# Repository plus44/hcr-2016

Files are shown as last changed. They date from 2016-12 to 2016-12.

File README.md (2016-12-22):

# Human-Centred Robotics 2016

##### Xavier Laguerta-Soler, Periklis Korkontzelos, Nathan Warner, Mihnea Rusu
##### {xl5512, pk1913, njw13, mr3313}@ic.ac.uk
##### *Imperial College London*

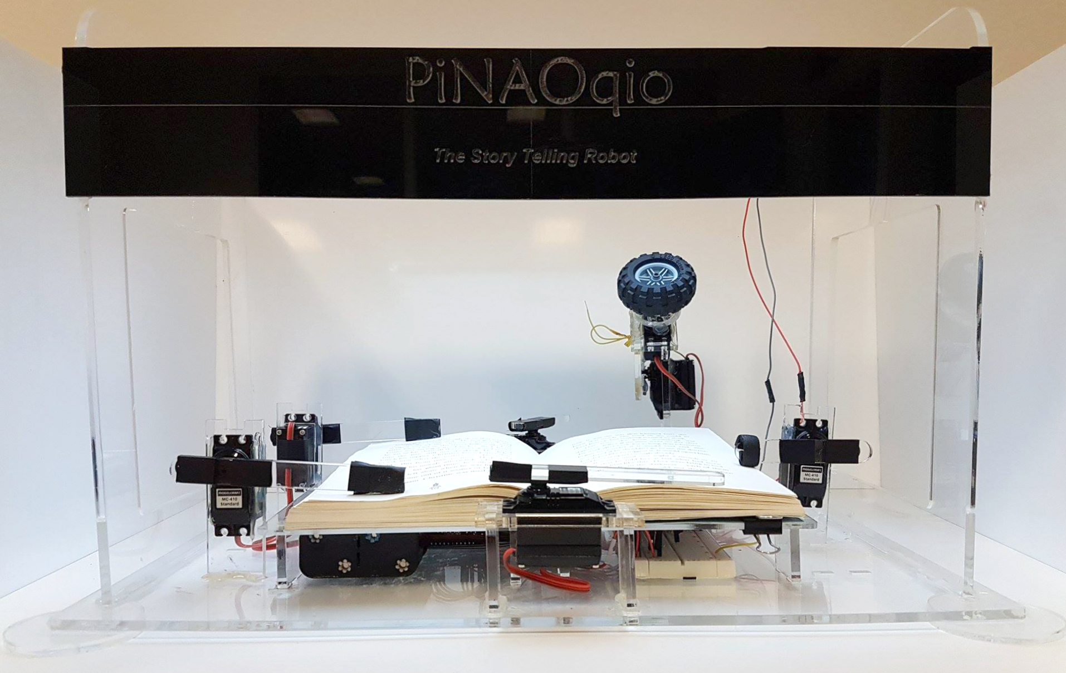
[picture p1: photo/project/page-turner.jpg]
PiNAOqio Page Turner (https://www.youtube.com/watch?v=8CyoGCQ_uKY)

Video :video_camera: link: https://www.youtube.com/watch?v=8CyoGCQ_uKY

Our project is about building an interactive story-telling robot that reads (and turns the pages of) physical books to children :baby:. Our robot, **PiNAOqio**, uses the [NAO robot](https://www.ald.softbankrobotics.com/en/cool-robots/nao) from SoftBank Robotics to interact with the reader through speech and gestures. An additional hardware rig was designed and built to turn the pages of books and to accommodate a camera for capturing the open leaf. 

As this was first and foremost a research project, we set out to test the hypotheses proposed in our initial report, the [design report](docs/reports/design-report.pdf). Evaluation sessions were held, where participants were presented with 3 different instances of our system with varying degrees of capability and were read a short passage from the same book :book: by each. In response, their task was to complete a brief questionnaire.

The full system is comprised of the following components: a laptop :computer: to interface with NAO, the robot, and to perform optical character recognition (OCR) on the picture of the book; a Raspberry Pi to control the page-turning mechanism; an iPhone :iphone: (6 or higher) to photograph the open book, and a server on the cloud to enable communication between the different platforms. As will be apparent to the reader, our system architecture ended up being quite different (and more complex) in the [final report](docs/reports/final-report.pdf) to what we initially envisioned in the design report, mainly due to complications with the OCR setup.

Ultimately the project was a success :clap: - the high-risk components namely the page-turning mechanism and OCR functioned to a high standard and the results of our research suggested the proposed hypotheses :+1:.

## Contents

This repository is composed of the following directories:
  - **[app](app)** iOS app source code and Carthage dependencies.
  - **[docs](docs)** System startup documentation and reports written for this project (including the individual reports).
  - **[eval](eval)** Evaluation questionnaires handed out to the participants of our study and a Matlab script to determine the results of our experiment.
  - **[hardware](hardware)** Laser cutting files for the page-turner.
  - **[scripts](scripts)** A number of useful, but maybe messier scripts for quick or intermediate testing.
  - **[sdk](sdk)** The correct version of the NAOqi SDK that works with Python.
  - **[src](src)** Source code (in Python) for all individual elements of the system, along with a pip requirements file for setting up (a partially working) virtual environment. Each component is meant to have a copy of its respective subdirectory. The [phone](src/phone) component is only a networking-enabled dummy, as the real phone component is the iOS app.
  - **[photo](photo)** Test photographs of various book poses and lightings (for OCR) taken throughout the course of our project, along with a dedicated file, *[latest.jpeg](photo/latest.jpeg)*, that the laptop client updates while it's running, with fresh images received from the phone.

Link to the Python library used for [speech](https://pypi.python.org/pypi/SpeechRecognition/), which is not included in our virtual environment requirements file due to platform mish-mash :disappointed:.

### Quick links:
  - [Design Report](docs/reports/design-report.pdf)
  - [Final Report](docs/reports/final-report.pdf)

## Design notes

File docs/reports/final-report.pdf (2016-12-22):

## PiNAOqio: Research into Interactive Story-Telling Using Robots and Physical Books

Xavier Laguarta Soler (xl5512), Periklis Korkontzelos (pk1913), Nathan Warner (njw13), Mihnea Rusu (mr3313) Imperial College London

Abstract
This paper evaluates the effectiveness of the interactive
robot storyteller PiNAOqio, boasting the ability to turn the pages of physical books and deliver contextualized gesticulations. An assessment was conducted on 23 volunteers whereby PiNAOqio was pitted against both a static implementation and an audiobook. Performance was measured in terms of information retention and user enjoyment, finding PiNAOqio to be just as, if not more effective than the audiobook across our given test population. Further developments and enhancements are proposed to be implemented in the near future.
I. Introduction
Reading is an integral and fundamental aspect of a child’s education and has been shown to have a significant influence on their development (Freire & Slover, 1983). In today’s digital era the ways through which children are
introduced | to | books | and | written | content
is constantly evolving, placing an increasing prevalence on digitized content and stepping away from traditional hard-copy books. PiNAOqio proposes a new and innovative means to bridge this gap and engage children with literature. Utilizing a synergistic collaboration of an automated page turner, optical character recognition (OCR) algorithm, intelligent gesture association engine and voice recognition, PiNAOqio is well poised to revolutionize conventional story time.
With users being able to load their own pre-existing volumes, PiNAOqio will be versatile enough to be deployed in a range of situations and environments. We feel that children that have to be hospitalized for long periods of time, in particular, would stand to receive the greatest benefit from this technology. Not only
will PiNAOqio be | able | to | read | them
their favourite stories, he can also serve as a companion, supplementing the limited human interaction they are likely to receive and alleviating some of the stress and anxiety these children are prone to experience (Lau, Bernard and Wilson, 1993). Although PiNAOqio is not intended to be a tantamount replacement to a genuine human storyteller, he is anticipated to make story telling a more fun and social experience for young listeners.

II. Hypothesis
The aim of this project was to investigate the effectiveness of a “storyteller robot” as a source of engagement and educational entertainment for children. In order to quantify whether this goal has been achieved, user experience and the ability to retain information were measured. Upon this basis, the subsequent hypotheses are assessed. These figures have been approximated to indicate thresholds for satisfactory performance:
a) Story-telling by PiNAOqio will improve information retention and user experience by 15% and 30% respectively in comparison with story-telling by an audiobook.
b) Making gestures to emulate a human story-teller in conjunction with an active interaction with the user will improve the retention of information and the user experience by 10% and 20% respectively.

III. Related Work
The concept of an interactive storytelling robot has been approached by other groups in the past; equally, there exist several page flipping mechanisms for the purpose of digitizing hard copy books (Qumsiyeh, 2016 and Charlton, 2015). However, an implementation that uses both of these in tandem has heretofore not been attempted.
An instance of a comparable system, The Storytelling Companion, designed by the Personal Robotics Group at MIT (Kory, 2016), was developed as a social character relating to children as a peer through a storytelling game. This game is played on a tablet and the aim is to improve language and vocabulary skills in early stages in life. Another example is TROBO – the storytellinsg robot (TROBO, 2016), a plushy robot that connects to a smartphone or tablet application and tells an education story from a library.
The fundamental drawback to these currently available solutions is that they rely on a tablet to function. Long-term use of tablets and other such devices have been shown to have a detrimental impact on young children, such as addiction. The positive to this approach is that it utilizes technology the user is already likely to own, thereby largely reducing the overall cost of the product.

IV. System Design

### 1. Overview

From our previous report (Laguerta, Korkontzelos, Warner, & Rusu, 2016), the system has increased in complexity as we discovered insufficiencies with the old setup that would disrupt our desired user experience. Formerly we decided that a Raspberry Pi 3 should act as the main controller, communicating with the NAO robot, page-turning mechanism and camera. Such a setup would have been simpler to execute, and would have yielded a more portable prototype at the cost of limited opportunity for expansion and improvement past basic functionality. The major problem with this setup was the poor quality of the official Raspberry Pi camera for our purpose of optical character recognition (OCR).
Our first attempt at solving the problem of the camera, mentioned in one of our individual reports (Rusu, 2016), was to install a light-plate fashioned from a liquid crystal display (LCD) backlight directly above the book. While this boosted the accuracy of OCR slightly, we were still troubled by the shallow depth of field of our camera, which made it so that only a handful of pages could be turned before a (manual) refocus was needed. After experimenting with exposure settings and filter parameters on the Raspberry Pi camera, we were ultimately unable to produce reliable, repeatable OCR results.
Brief experimentation with an iPhone camera using the existing rig resulted in OCR accuracy figures of approximately 90% following brightness and contrast image enhancement filters. This observation led to our decision of using a smartphone as the camera, despite the increase in system complexity posed. At this point, the Raspberry Pi was only required for controlling the page-turning action; as such, we decided it would be best that a laptop with far more computational power than a singleboard computer handled the OCR engine and communications to the NAO robot. An iOS app would be needed, as well as a means for transmitting images from the phone to the laptop and page-turning instructions from the laptop to the Pi board.
The final system was comprised of five elements: iPhone, Raspberry Pi, laptop, the NAO robot, and a server running on the cloud as an Amazon Web Services (AWS) instance to enable communication between the components. A high-level diagram of the system is shown in figure 1. Communication to the server is done via (Hypertext Transfer Protocol) HTTP. The role of the server is to manage the data being transmitted to each serverconnected device given what has been received from all devices up to that point in time.
Devices operate in half-duplex mode: either transmitting or receiving. During autonomous system operation only two of three devices should ever be simultaneously in receive mode on the network, otherwise the system reaches rest. Receive mode utilizes a technique known as HTTP long-polling that reduces the amount of unnecessary network traffic when polling for data. The client begins by sending a request for data from the server, to which the server only responds after data is available for that device or a time-out has occurred (in which case the request should be re-initiated). Devices expect to receive single actions from the server, thus the data being transmitted is simply the action, or data object (e.g. image) as a string. Transmission data is sent using (JavaScript Object Notation) JSON strings in the body of the HTTP requests.

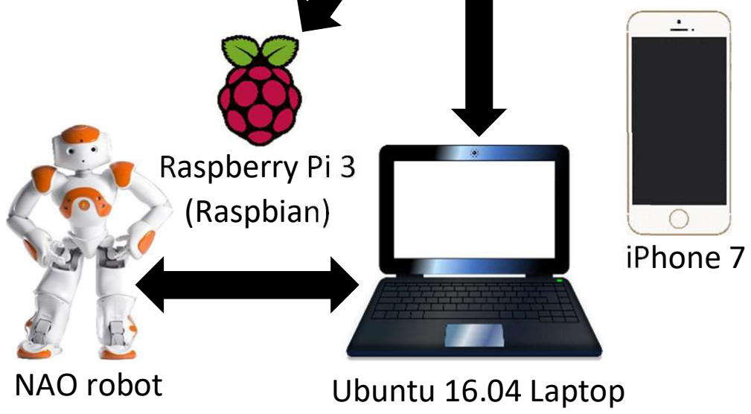
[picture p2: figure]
Raspberry Pi 3 (Raspbian); iPhone 7; NAO robot; Ubuntu 16.04 Laptop

### 2. Server

The elements of our system need a way of communicating with each other in an organized manner in order to emulate the behavior of a state machine. One thing all our components have in common is a network connection – the obvious facilitator for our goal is thus a centralized hub (or server) to which all devices report updates to their state. A t2.micro Elastic Compute 2 (EC2) instance on AWS running Ubuntu 16.04 was used as the platform for our server. The cloud server route was taken due to the hosting restrictions imposed on the college network. With access to an isolated network, the server component can be integrated within the laptop component and the system design simplified.
Python was used to implement a multithreaded HTTP server with three valid addresses: /pi, /phone and /laptop. The HTTP protocol defines several possible request types

AWS Server

Figure 1 - System High Level Diagram that may be sent by a client device. Of importance for our application are the GET and POST requests. A GET request to one of the aforementioned addresses initiates the long-polling process, and the server would only fulfill the request if data is available for that device or the time-out threshold has been reached. Multithreading is necessary for handling long-polling as this is a blocking operation, meaning the thread of execution is blocked until a result is available. POST requests from a device to the server contain JSON data about the state of that device. The JSON fields are specific to each device and are agreed upon by both the client and the server before runtime.
State machine functionality is emulated on the server through (First In First Out) FIFO queues. JSON data combinations from a device’s POST request produce one or more work items, or actions, that need to be passed on to the other devices. Each device has its own FIFO queue of work items; the resulting actions are pushed on the corresponding device’s queue. When a device long-polls the server and its queue is not empty, the first element on its queue is popped and parsed in the body of the HTTP response.
Emulating a state machine as such offers a high degree of modularity and flexibility in adding functionality to the system as a whole. Additional JSON fields may be defined for a device, as well as the work items they generate. Handling the new functionality can be implemented simply on the respective target device side

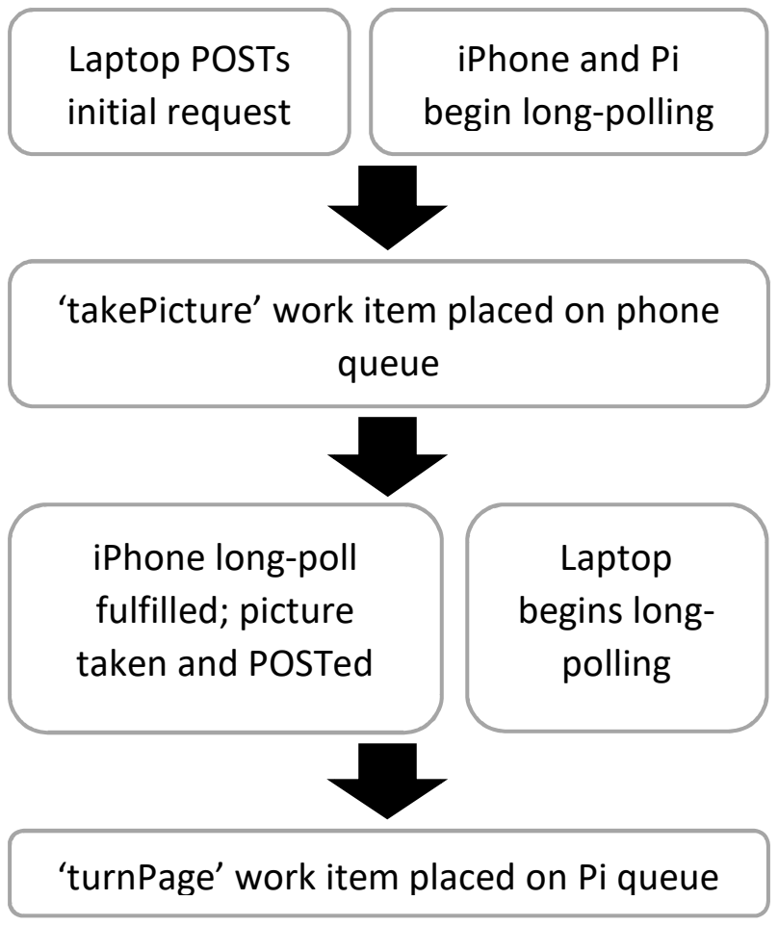
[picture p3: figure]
Laptop POSTs initial request; iPhone and Pi begin long-polling; ‘takePicture’ work item placed on phone queue; iPhone long-poll fulfilled; picture taken and POSTed; Laptop begins long- polling; ‘turnPage’ work item placed on Pi queue

by scripting the desired action in response to the received work item. Before deploying the server, we first ensured successful operation using dummy clients on the physical laptop. Example operation from rest is briefly shown in figure 2.

### 3. iPhone App

There are two main tasks the iPhone element of the project must perform: capture and filter an image using the rear-facing camera; and implement the functionalities of the phone client. A skeleton camera app, written in Swift, provided by an online article [Caldari, 2015] was used as a starting point. Since modern iPhones feature powerful Graphics Processing Units (GPUs), we decided to take advantage of said feature by firstly configuring the base app to use the GPU pathway for rendering the image, and secondly to filter the shot on the GPU. This enabled a real-time post-filtering viewfinder that did not introduce any visible lag to the graphical user interface (GUI), even on an older generation GPU-equipped handset.
In terms of image filtering, the Apple iOS Core Image library provides a large number of GPU filters, with easily configurable parameters as well as the option of userwritten kernels in a limited version of the OpenGL language. Our final filter stack was composed of a saturation reduction filter (for converting the image to black and white), followed by brightness and contrast booster filters and ending in a custom GPU kernel for a thresholding filter. The thresholding filter determines whether the intensity of a given pixel is below or above one of two thresholds. When below the respective threshold, the pixel is forced to black; when above, the pixel becomes white. Even without our dedicated lighting rig, OCR accuracy levels of 100% were common occurrences in our experiments, proving to us that switching to the iPhone camera was indeed the right choice.
Client-side code was written using the aid of the Alamofire networking library and the SwiftyJSON library for generating the JSON inside the POST request to the server. Instructions for only a single server action were provided – ‘takePicture’, and only a small number of data fields were required. The filtered image was sent across to the server as a base-64 encoded string in the JPEG format with minimal compression factor, under the ‘picture’ data field of the JSON POST request. Previously (Rusu, 2016), we mentioned requiring lossless compression for the picture on the Raspberry Pi camera, however this proved to be unnecessary in the case of the higher quality iPhone camera.

### 4. Raspberry Pi

The main role of the Raspberry Pi is to sequence the servos of the page turner in order to flip pages of the book, when instructed to do so by the server. A secondary role

Figure 2 - Example System Operation of the Pi is to control the brightness of the lightplate in order to improve OCR performance. However, given the speed and accuracy of the iPhone camera’s auto-exposure function and the performance of our filter stack, we found that the only use of this functionality is to preserve battery life. In the final prototype, the Pi was not to be connected to a screen, mouse or keyboard therefore we created passthrough modes on the server and laptop sides that would allow control over it out of story-telling context. Multithreading was used to enable control of several servos in parallel. One problem we faced was with the built-in (General Purpose Input-Output) GPIO library on the Raspberry Pi. This library is not designed for multithreaded operation, and as a result we were troubled by segmentation faults when trying to access the same servo multiple times in a program. Happily, the solution was simple - run each set of parallel servo operations as a standalone script.
As in the case for the other devices on our network, the Pi requires client-side code that mirrors what the server expects from it and reacts to all possible actions received from the server. Since the mechanics of the page flipper have no way of feedback, a way for the laptop to adjust a small set of servo parameters was needed as the robot would reach further into the book. Fortunately, the software architecture allowed us to implement this with ease, by defining new work items for the Raspberry Pi, together with the corresponding JSON fields on the laptop side.

### 5. Laptop

Arguably the central element of our system was the laptop. Its responsibilities included: speech processing the user’s voice greetings and commands through an external microphone; requesting images from the server; doing OCR on images of text from the book; parsing gestures into the text obtained from OCR; and lastly controlling the NAO robot. A state machine was in charge of requesting server data and performing the operations in the needed order.
As for the case of the Raspberry Pi and the server, Python was used for writing the laptop code. The C++ based OCR engine Tesseract proposed in the analysis of one of our individual reports (Rusu, 2016) was used in the final prototype. Thanks to the library’s popularity in the open-source community, a Python wrapper was readily available for it. An outdated version of the NAOqi Python Software Development Kit (SDK) was used, as the most recent official one at the time of writing was not functional. Thankfully, we were not missing any features of the newer library to complete our project. Finally, user speech processing was handled using the latest official Python Speech Processing library.
In our design report (Laguerta, Korkontzelos, Warner, & Rusu, 2016) we mentioned the need for doing the page turn and OCR with a short time in advance such that NAO can speak without interruptions. Due to NAO’s speaking and OCR being blocking operations, multithreading was required to achieve this purpose. Unfortunately, due to time constraints with the project we were unable to implement this feature. However, thanks to the high performance laptop used, the delay between an image being received and OCR being complete was reduced compared to the alpha prototype featuring the Raspberry Pi as the main controller.

### 6. Page Flipper

The page flipper module is required to flip the pages of the loaded volume once it receives its cue from the server, allowing for a seamless transition in the flow of the passage. Each turned page will need to be presentable enough for OCR to take place, entailing minimal creasing and curvature. A custom servo actuated mechanism was designed and built, with each servo operated sequentially, modelled as a state machine on the raspberry Pi. The system receives an action request from the server, the sequence executes and then awaits its next command. The sequence is shown in figure 3, below.

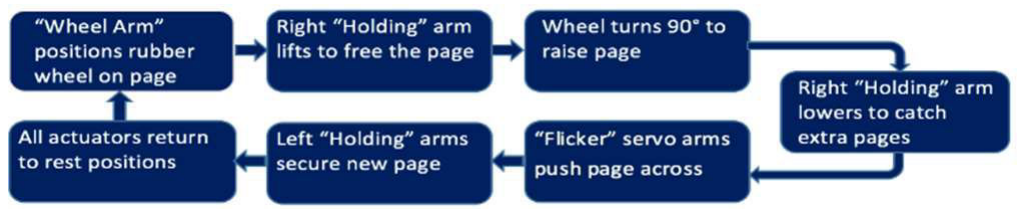
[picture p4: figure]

Figure 3 - Page Turning Sequence for Servos
The pivotal component of the system is a small rubber wheel that produces traction in order to lift the page. After passing through several iterations and permutations, the final mechanism to accomplish the page turning utilised seven servo actuators, these are illustrated in figure 4.

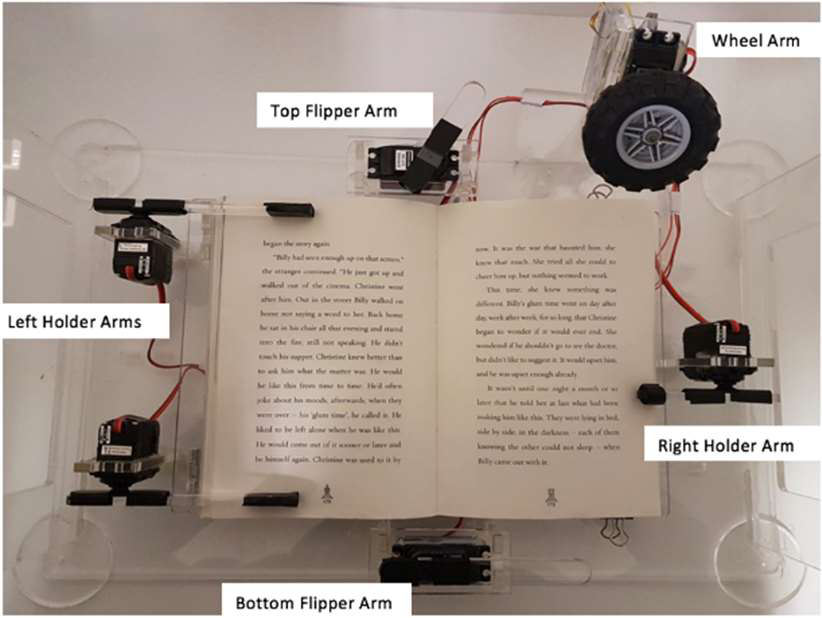
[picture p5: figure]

Figure 4 - Final Design of Page Turning Module

The whole module was made wireless and portable, using an 11.1V Lithium Polymer battery to power the light plate, with a 5V buck converter to supply both the servos and Pi. The entire assembly was constructed from 5mm laser cut acrylic, allowing for both a stylistically pleasing and structurally functional design, as well as fast development time. Once loaded by the user with any standard size fiction text and properly calibrated, the system was capable of autonomously turning in excess of

### 10 consecutive pages without error. The final system

assembly is shown in the appendix.
Although the page flipping was shown to work well, there are several potential enhancements through which the performance could be improved significantly. Namely, feedback could be introduced on the wheel using a micro load cell, allowing it to consistently assert the appropriate amount of force on the page. For testing the ideal wheel height was determined experimentally, programmed into the system and adjusted as needed. The drawback to this approach is that the angle by which the wheel came down by had to be user adjusted every 10 pages or so as this height changes. Another weakness with the current configuration is that there is considerable jitter in the servos. Since we are using a software based controller, the timing of the pulses sent to the servos is likely to be thrown off by other processes running on the operating system. To circumvent this, it would be advantageous to control the servos instead using hardware; this can be done using a dedicated PWM chip, such as PCA9685 that interfaces directly with the Pi via hardware I2C.
In addition, with the current setup two or more pages may be turned at once due to irregularities in the binding of the book, pages being stuck together, or the wheel asserting too much force. Currently the system has no means to deal with this eventuality. One possible approach could be to keep track of the page numbers involves the OCR module. If an inconsistency in the page count is detected, PiNAOqio can then alert and instruct the user to turn back to the correct page. Better yet would be the ability to actively check and detect whether more than one page has been lifted and turn back to prevent the error from occurring. Commercial printers are faced with a similar challenge, some transmit ultrasound through the page and measure the transmission coefficient, thereby any discrepancy in this reading can trigger an error condition.

### 7. Gesture Controller

The NAO robot is controlled by a gesture controller, which is implemented as a python class. The gesture controller interfaces between the laptop and the robot and is responsible for implementing all talking and gestures made by PiNAOqio during initial interaction and storytelling, using the API (Aldebaran, 2016) provided by Aldebaran.

The gesture controller is initialized along with the main program at the initialization of the main state machine. In the initialization phase the motors of the robot turn and PiNAOqio stands up to signal the user that testing is about to commence. In addition, the desired pitch, speed and volume are set to their default value.
For the initial interaction, the gesture controller is passed to the speech controller module and called upon whenever needed, to avoid the risk of runtime errors whereby more than one modules try to access the NAO robot. The questions and responses of PiNAOqio during this phase are predetermined and thus, a text-to-speech function handles the articulation of responses. At the same time, the BodyLanguageMode is set to ‘contextual’ and allows the robot to make gestures that can be associated with the responses given. This is a built-in function from the NAOqi API and works on a basis of a dictionary associating words with gestures. This is not optimal as some gestures appear to be out of context, yet it enhances the animacy and likability of the robot, which is the aim. During storytelling, the gesture controller is being used for the fully interactive and the non-interactive robot versions. For the non-interactive version, only the text-tospeech function is being used as no gestures are required. In order to acquire statistically meaningful data for the evaluation of the hypothesis, it is required that the fully interactive version PiNAOqio emulates a human storyteller as closely as possible. Thus, the
‘contextual’ BodyLanguageMode is | not | adequate
but two more dictionaries associating key words/phrases with gestures are built to provide a more refined gesture library. The first library is built using some already available gestures that accompany words such as “me”, “you” and “I don’t know”. To further enhance the animacy of PiNAOqio custom gestures are added by defining joint angles as a function of time through choreograph. These gestures are more specific and complex to generate including gestures to “wipe forehead” or change eye colour LED, so the custom dictionary was optimized for the specific, fully-interactive passage.
A string parsing algorithm has also been developed as part of the gesture controller and is responsible for handling the gestures of custom built dictionaries. Before the interactive storytelling commences, the story string is parsed according to key words and phrases of the two dictionaries. The gesture controller is then able to determine the timing and the place to input gestures associated with speech.

### 8. Speech Recognition

A speech interaction component, Speech Controller, was introduced to the interactive version of the robot before the reading began. Aside from basic salutations, the interaction allowed for the robot to get feedback on the user whether the volume and speed were fine or should be changed before the reading began.
This was implemented as a python class, which was called from the main state machine at an initial stage. Google speech was used as the speech processing tool, as it gave the highest accuracy when compared to other easy to implement tools, such as sphinx. Once the speech was recognized, the string of text was checked with a dictionary in order to detect the key words in each sentence, which varied as the conversation progressed. Depending on the result, one answer or another would be given by the robot, along with a specific action if required, such as increasing the volume or speed of speech.
V. Experiment
Pinaoqio was tested over the course of three days in room 508 of the EEE building in Imperial College London to have a testing environment of complete silence. Keeping a low noise level was important for the reliable operation of the speech recognition module, but also to make the story-telling experience more enjoyable by reducing distractions.
The book of choice was "An Eagle in the Snow" by Michael Morpurgo, primarily because it is a child’s book. However, this book also has large font and thick pages facilitating optimal performance of the pageflipping and OCR modules. The testing consisted of reading three passages of the book, firstly using an audiobook recording taken from Audible, secondly a fully interactive PiNAOqio with gestures and speech
recognition and | finally, | a | non-
interactive PiNAOqio version. Each of these methods consisted of different story telling versions that were then compared. The passages were also chosen so that there is a logical link between them and to allow the user to follow the story.
After each passage, a questionnaire was completed by the users to test the text comprehension of that passage and
the | user | experience | for | the | version
used. The questionnaire was organized into three main sections, covering personal information (age, sex, robot exposure), passage comprehension and information retention through multiple choice questions and user experience through a semantic differential scale assessing Animacy, Likability, Perceived Intelligence and Safety.

VI. Results
Of the 23 people that participated in the experiment, the average age was 20.35, with a standard deviation of 1.41. From the whole population, 26.1% were females and the rest males. On average, the users that undertook the evaluation session read 10.41 books annually, so one could argue in favour of a familiarity with books.
The results can be broken down into two main sections: information retention and user experience. For information retention, users had to answer four multiplechoice questions for each passage and their score is determined as a percentage. User experience on the other hand, is assessed through a semantic differential scale, in which users were asked to indicate their position on a scale between two bipolar words, the anchors (Bartneck et al., 2008). This scale measured the user experience for the narrators’ Animacy, Likeability, Perceived Intelligence and Perceived Safety on a scale of 30, 25, 25 and 15 respectively. Furthermore, for the user experience results were separated into different groups according to gender and robot experience in order to investigate any correlation between a group and an experience.
The results are summarized below, in table 1.
| Audiobook | Interactive | Non-Interactive
Information Retention (%) | 73.53 | 77.94 | 58.82
Animacy (/30) | 19.88 | 21.59 | 12.53
Likability (/25) | 18.11 | 20.35 | 15.94
Perceived Intelligence (/25) | 18.76 | 18.12 | 15.41
Safety (/15) | 10.47 | 11.12 | 9.65
Averages (/95) | 67.22 | 71.18 | 53.53
Male UX (/95) | 67.77 | 71.92 | 53.54
Female UX (/95) | 65.5 | 81.75 | 53.5
Robot Exp. 1 UX (/95) | 68.75 | 74.5 | 53.25
Robot Exp. 2 UX (/95) | 71.25 | 70.75 | 57.75
Robot Exp. 3 UX (/95) | 64 | 70.63 | 50.75
Robot Exp. 4 UX (/95) | 71 | 64 | 60
Robot Exp. 5 UX (/95) | n/a | n/a | n/a

Table 1 - Results

VII. Discussion
According to the hypothesis, the fully-interactive version of narration implemented by PiNAOqio would improve amount of information processed and remembered and also enhance the user experience compared to both the audiobook version and the non-interactive version. Based on the above results, the validity and accuracy of our hypothesis is evaluated, while an attempt is also made to explain the factors leading to such results.
In terms of information retention, the interactive version entails the highest percentage of correct answers with 77.94% of them being correct, 4.41% more than the audiobook version and 19.12% more than the non-interactive version. When comparing the interactive with the non-interactive versions, it is expected that any variation is a result of the additional gestures implemented of the former. This results supports the Social Agency Theory, according to which the combined effect of multiple interaction techniques exceeds the
individual | effect | of | each | one
(Ham, Bokhorst & Cabibihan, 2011). Moreover, the difference between the audiobook and the fully interactive version is not as significant. While, gesturing creates a more rounded experience engaging vision in addition to hearing, the voice used by PiNAOqio is not able to achieve the same expressive articulation used in the audiobook. In fact, being narrated by a professional
human | storyteller, | the | audiobook
incorporates emphasis at critical point, pauses for dramatic effect and other narration tools to enhance the storytelling experience. It is interesting to note, that the benefit of adding gestures outweighs the drawback of using a what some called a “robotic voice” lacking the natural aptitude of expression.
The fully interactive version also had the highest ranking in the overall user experience evaluation, 4.17% and 18.58% more compared to the audiobook and non-interactive versions, respectively. It also ranks the highest in the subcomponents of Animacy, Likability and Perceived Safety, while it only lags to the audiobook in terms of Perceived Intelligence. There were two main factors contributing to that; firstly, the interaction designed was relatively straightforward, not including a refined artificial intelligence module to interact with user. Moreover, at certain point during storytelling by PiNAOqio, pauses would be inserted into incorrect positions, thus making the robot appear less intelligent. An interesting result emerges by separating the group by sex. While the overall user experience, including Animacy, Likability, Intelligence and Safety, is approximately the same for both males and females in the audiobook and non-interactive versions, this is not the case for the fully interactive version. Females, ranked the user experience for the latter with an average of 81.75/95, which 10.3% higher than the males’ average score. This could be explained by the appearance of the robot which appeals more to the female population, possibly due to the ‘cuteness’ factor of the robot being appreciated more. However, since the female population was only 26.1% of the total population, more data would be required to present a statistically significant result.
A final point that can be drawn from the results of the evaluation session has to do with user experience as a function of exposure to robots. For the fully interactive version, which is the one with the most added functionalities, there seems to be a clear, negative relationship between user experience and exposure to robots. People that are more familiar with robots are less fascinated by features they have already seen and experienced and are more likely to notice an inconsistency or a malfunction. These two factors contribute to the decline of user experience by 11.1% as robot exposure increases from 1 to 4 on a scale of 5, as shown in table 1.

VIII. Future Work
Despite the success of the project in building a system which is more than adequate to be tested on users and support the main hypothesis, there are still opportunities for further enhancements. Further work could be carried out to make the robot smarter, perform a quantitative engineering analysis on users and compare the system with state-of-the-art rival systems.
A major difference between PiNAOqio and a human storyteller is the ability of the human to interpret literary tools used by the author to convey meaning. One solution for making PiNAOqio ‘smarter’ could including saving the text read by the OCR module in memory and using it for future user-interaction. Currently, strings are fed to PiNAOqio to tell the story and are then discarded, which makes it impossible to acquire a generic perspective. If, however, larger passages were being stored, then more refined algorithms could be developed aiming to grasp the main points of the book, such as who is the main character and the mood of the story. Thereafter, PiNAOqio could engage in a more personal manner with the user, asking him questions specific to the
story. | It | is | expected, | that | by
enhancing PiNAOqio’s functionalities, it will be able to emulate a human storyteller more closely and provide a better experience to the user.
While a lot of care was put into making a fair questionnaire, this method of evaluating a system will always withhold some degree of subjectivity. A questionnaire would be even less reliable in the case of the system being evaluated on children, as they are less likely to be objective when completing it due to their lack of interest [Goodman, 2001]. Another measure of user experience involving emphasis in engineering techniques could include recording the motions of the user during storytelling as well as his gaze and pupil dilation. Looking at the overall motion of the user during storytelling could be indicative of the attention he is paying at the narrator while tracking gaze and pupil dilation could provide a measure of the user’s interest in the story (Wang, 2009). Finally, through research of the relevant work in the area of robotic storytelling, the avatar storyteller version has been identified as the most commonly implemented solution. This is mainly due to the low cost of a virtual storyteller which can be implemented in the form of a tablet application, compared to an actual robot associated with significant fixed costs. By comparing our proposed solution with the current benchmark for a virtual storyteller, we would be in a position to assess whether the development of a robotic storyteller is a viable project in the market and what is the true value added by this implementation.

IX. Conclusion
PiNAOqio is designed to provide educational entertainment for young people that would otherwise be at risk from the adverse effects of long-term use of electronic devices. It consists of a novel storytelling system using the NAO robot, a page flipper and an OCR module to read physical books. After being tested, it was found that the fully interactive version improves information retention by 4.41% and 19.12% and user experience by 4.17% and 18.58%, compared to audiobook and non-interactive version, respectively. Further enhancements are being proposed to improve the intelligence of PiNAOqio, perform a quantitative analysis of results and to test the system against an avatar solution.
X. References
1. Bartneck, C., Kulić, D., Croft, E. and Zoghbi,
S. (2008). Measurement Instruments for the
| Anthropomorphism, Animacy, Likeability, Perceived Intelligence, and Perceived Safety of Robots. International Journal of Social Robotics, 1(1), pp.71-81.

### 2. Wang, Joseph. (2009). Pupil Dilatation And

| Eye Tracking.

### 3. Kory, Jaqueline. (2016) Storytelling

| Companion - Personal Robots Group. Personal Robots Group, 2016. Web. 28 Oct. 2016.

### 4. TROBO. (2016). TROBO The Storytelling

| Robot: What Are Trobos?

### 5. Aldebaran. (2016). Naoqi Apis — Aldebaran

| 2.1.4.1 Documentation. Doc.aldebaran.com

### 6. Goodman, Robert. (2001). Psychometric

| Properties of the Strengths and Difficulties Questionnaire. Journal of the American

Academy of Child & Adolescent Psychiatry, 40(11), pp.1337-1345.

### 7. Qumsiyeh, D. (2016). Linear Book Scanner -

The open-source automatic book
scanner. Linearbookscanner.org, [Online]. Available: https://linearbookscanner.org. [Accessed: 17- Nov- 2016].
8. (2016). Book scanner ScanRobot® 2.0 MDS -The automatic page turner
solution. Treventus.com, [Online]. Available: http://www.treventus.com/automatic-bookscanner-scanrobot.html. [Accessed: 17- Nov-2016].

### 9. M. Dredge, T. Stuart. (2013). Children's

Reading Shrinking Due To Apps, Games And Youtube. The Guardian.

### 10. Laguerta, X., Korkontzelos, P., Warner, N., &

Rusu, M. (2016). PiNAOqio: Story-telling for children using physical books and HRI. Imperial College London.
11. Caldari, M. (2015). Camera Capture on iOS. Objc.

### 12. Charlton, J. (2015). Mechanical System For

Lifting And Turning Bound Pages. Web. [Accessed: 28 Oct. 2016].

### 13. Rusu, M. (2016). Making PiNAOqio Read:

Digitizing Text From Physical Books. Imperial College London.
14. W. K. Lau, Bernard and Wilson W. C. Tse. (1993).Hospitalised Childer Stress: Psychologi cal Effect Of Physical Illness And Hospitalization On The Child And The Family.

### 15. Freire P., & Slover, L. (1983). The Importance

of the Act of Reading. The Journal of Education 165(1).
XI. Appendix

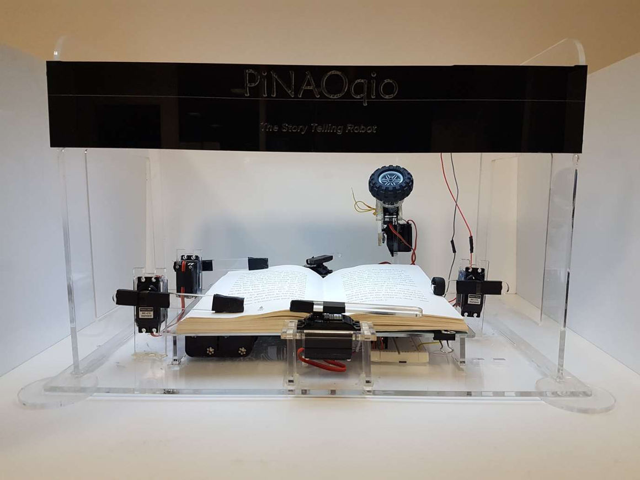
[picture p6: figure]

Figure 5 - Final System Assembly

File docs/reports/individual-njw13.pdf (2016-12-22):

## Making PiNAOqio Read: Turning the Pages of a Physical Book

Nathan Warner (njw13)
Imperial College London

Abstract: In this report I outline the challenges associated with enabling PiNAOqio to read from and turn the pages of real books. Several existing devices that accomplish similar functions will be discussed followed by an in depth overview of our proposed servo actuated mechanism. The progress thus far in its implementation will also be shown.

I. INTRODUCTION

Currently on the market there exist a number of story telling robots [1]; each of these however relies on the use of tablets loaded with e-books. It has been shown that prolonged use of tablets can have a detrimental impact on young children [2,3]. In addition, if children are introduced to literature in a purely digital format it may deter them from reading physical books later in life. Heretofore, the concept of an interactive robot story teller that can read physical books is a niche that has not been explored.

One of the toughest challenges in realizing the PiNAOqio storyteller robot is his ability to turn the pages of real books. This proves difficult to achieve reliably since the operation requires many degrees of freedom each with accurate synchronization. In addition, there is the variability imposed by the dimensions of different books. After researching existing page turning systems, we devised a bespoke mechanism that utilizes an arrangement of servos configured as a state machine and controlled by the Raspberry Pi.

II. REQUIREMENTS

The page flipper mechanism will be responsible for turning the pages of the loaded volume so that there is a seamless transition in the flow of the passage. In order to accomplish this goal, the system will need the following features. Firstly, the operation must be reliable; this means there should be minimal glitches, such as turning more than one page at once or failure to complete a page turn. Due to time constraints and complexity, it is expected that the system will fail occasionally and may need human intervention. However, with good design these instances should be made as rare as possible so as not to adversely affect the experiment. The next important feature is that the mechanism should not crease the pages. This is clearly undesirable for the owner of the book if it damaged by the reading process. Furthermore, the performance of he OCR algorithm is drastically reduced if the pages have any irregularities.

The total time to complete a page turn is another important consideration. In order to avoid dead-time, PiNAOqio can commence a page turn prior to reaching the end of a page. However, if the mechanism takes more than several seconds to complete a flip it may prove to be a distraction and may influence the results of out experiment, seeing as one of our dependent variable is information retention. At the same time, the pages should be turned in a manner that retains a humanoid characteristic; ideally not too fast, at a speed comparable to that of a human reader. Finally, the product should be safe and well suited for its intended use around small children.

III. RELATED WORK

Through our research we uncovered several existing mechanical solutions for turning the pages of physical books. Although nothing we found was directly comparable to our application and requirements, the following products contained aspects that had an influence on our final design.

Most notably the linear book scanner [4], a project that was initially started by google as a means of archiving physical books, but has since been adopted and developed further by several research groups [5]. The design consists of a prism shaped assembly upon which a face down book slides back and forth. Each time the book makes a pass a vacuum sucks a page from one side to the other. The book also passes over a scanner that digitizes both pages. This approach is optimized for scanning a large number of pages per hour with small error. It does not, however, retain any of the familiar human aspects of reading and requires a rather bulky assembly, therefore rendering it far from ideal for our project.

An accomplished commercial solution, the Treventus ScanRobot 2.0 MDS [6], can be purchased for $250,000 and is capable of scanning 2,500 pages per hour. The device has a scanning head that moves into the gutter of the book. Once there it applies a vacuum to suck up the page, as it moves up it scans the page, then once at the page edge the machine applies a blast of air to ensure the page falls to the correct side. This is a highly efficient and effective approach, although it isn’t suited to paperbacks as these do not sit open like hardbacks. There is also a high level of complexity involved; with an air blaster, vacuum pump and various stepper motors needed for its operation.

Another related project was undertaken by a team at the University of Ohio [7]. Their application was to assist sufferers of cerebral palsy in the turning of bound pages. The device that they developed consisted of a rubber wheel used to lift the page. Once lifted a turning arm would then push the page onto the opposite side. This approach was very simplistic requiring minimal external components. The shortfall is that the design only works with large textbooks style books, where the pages naturally fall to either side.

IV. IMPLEMENTATION

As shown by our research, there are a number of methodologies that we could deploy to accomplish the page flipping task. The three main ones we considered were based on either suction, pneumatics, servos and stepper motors, or a combination of these. We also divided the page flipping task itself into three sections and considered different methods for each: lifting the page, turning the page and holding down the page.

To generate the initial force to lift the page we could use a small vacuum pump to generate the suction. This approach is good in that it will be unlikely to crease the page. Although, if the interface with the page does not make good contact the vacuum may fail to lift the page; hence the reliability may not be great. This would also entail a high level of complexity with a number of custom 3d printed parts required.

Instead for the page lift section we decided to use a small rubber wheel, in the same way as the team at University of Ohio [7], that would make contact with the page and turn a small amount to raise the page. This wheel could be mounted on a servo arm to position it on the page then move it out of the way for the flip. Initial testing with such a wheel revealed this method to be rather effective, whilst also much simpler to implement. The rotation can be achieved either using a stepper motor or a continuous rotation servo.

Once lifted the page could be flipped using a blast of pressurized air similar to the ScanRobot 2.0 MDS. We decided against this; both because of the requirement for additional hardware, and since it will only prove effective on hardbacks or books with heavy pages. The implementation we decided to go with uses a flicker servo to catch the raised page and push it to the adjacent side. Since the page will not fall neatly on its own, a “digger arm” with two degrees of freedom will catch the page and assist it down. This should be more reliable as the page is guided through the entire path of travel. It also uses cheap and easy to control servos.

The final stage, holding the pages, would not be needed were we using textbooks or hardback books. The pages of paperback books on the other hand do not tend to fall open naturally, therefore needing assistance to be held flat. This also helps improve the accuracy of the OCR. The easiest way to achieve this would be to use holder servos on either side. These would be able both to push down to hold move up to release/accommodate a new page.

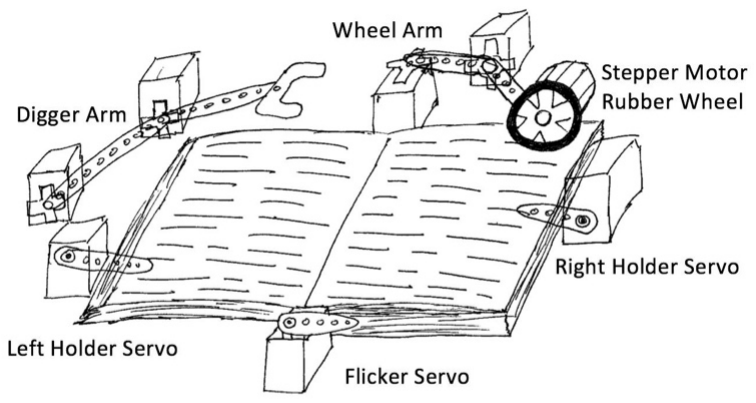
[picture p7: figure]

Figure 1: Page turning mechanism overview
V. ASSEMBLY

For the construction of the system we decided to use 5mm/3mm acrylic wherever possible and 3D printed PLA for more complex parts, such as the wheel mount. Acrylic was chosen because it is safe and easily cut using a laser cutter. The laser cutter also allows us to round any sharp corners that may be a hazard around small children. Acrylic is also more aesthetically appealing than other cheaper alternatives such as plywood; an important factor when the target audience is children and user enjoyment is critical to our hypothesis.

The servo we chose was the “Modelcraft RS 2 JR BMS-410C”, a plastic gear standard analogue servo. This model was chosen chiefly due to it’s cheap price, which was important seeing as we needed a large number, and also for its more than adequate torque of 35Ncm. Each servo is supplied with an arm containing mounting holes allowing for custom 3d printed/ laser cut parts to be attached.

Due to the large number of servos involved in the design it would be desirable to have a convenient way to mount them. The following servo brackets, shown in figure 2, were designed using laser cut acrylic that serve as a universal approach to mounting all the servos. These brackets neatly slot into pre-cut holes in the base avoiding the need for glue or bolts to hold it in place. Additionally, multiple holes can easily be cut at various different angles and locations. This enables us to quickly and easily tweak the positon of each servo for optimal performance. For instance, the angle at which the rubber wheel is positioned on the page or the distance of the digger arm from the book can be varied. This design greatly simplifies the the development process and makes prototyping much faster.

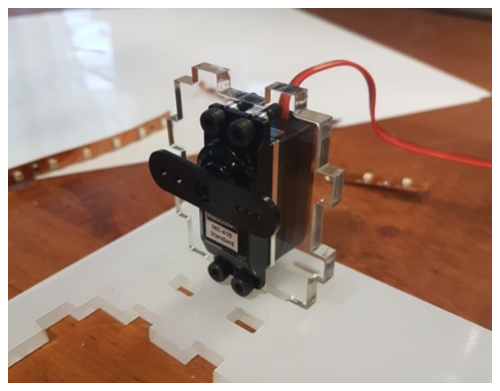
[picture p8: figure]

Figure 2: Universal Servo Bracket One issue that proved problematic in our design is that the heights of the front and rear covers can vary quite significantly as the pages are turned from beginning to end. To compensate for this, we decided to place each cover of the book on an independent platform. We considered using stepper motors to alter the level of each platform as the story progresses, however this would add a large amount of complexity to the design. Instead we chose to position each platform on a set of springs. This has the effect of lowering the heavier side with more pages, hence reducing the height disparity between the two sides.

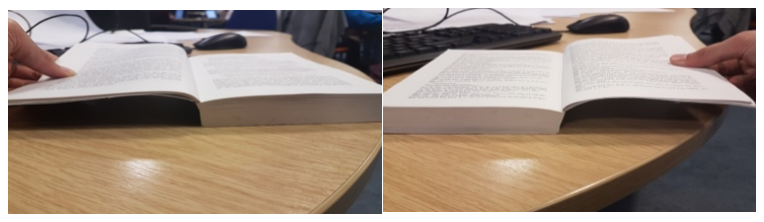
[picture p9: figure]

Figure 3a: Height difference of front and rear covers

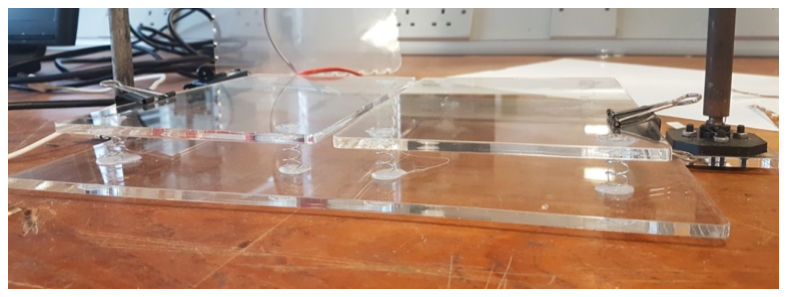
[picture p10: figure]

Figure 3b: Independent Spring Platforms

We constructed a preliminary setup as shown in figure
4. The purpose of this prototype was to determine the appropriate height at which to place the camera in order to achieve accurate OCR; this would then dictate the overall dimensions of the final revision. In order to conveniently vary the height of the camera, metal rods were attached to the base using 3d printed supports. Two smaller metal rods were then clamped to these, serving as a rail upon which the camera and pi assembly could slide along. The sliding was needed to assess whether OCR could be performed on both pages at once or if the camera would need to slide over each page individually.

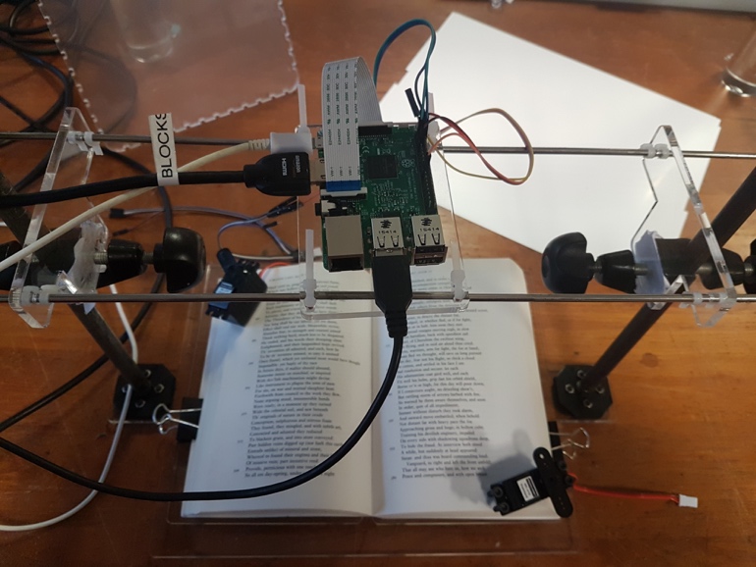
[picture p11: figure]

Figure 4: Initial Test Setup VII. SOFTWARE

The sequence of operation for each component of the system is illustrated in figure 5 and can be modelled as a state machine. Each servo is controlled via a PWM signal of 50Hz from a single GPIO pin, the duty cycle of this signal determines the position of the servo arm. For our selected servo model, a duty between 3.6 and 10.6% maps through an angle of 0 to 180˙.

The page turning event will be triggered once PiNAOqio is reading the final section of the second page. This could be initiated as the final block of text of sent to the NAOqi with a delay introduced if necessary.

Figure 5: Sequence of operation

IX. CONCLUSION

PiNAOqio is treading on uncharted territory with its ability to read hard copy books. Although a final prototype is yet to be completed, through the construction of a preliminary test setup we discovered the OCR to be effective form a single viewpoint of both pages. This was the main factor upon which the success of the project was contingent. We intend to start finalizing the design in the imminent future and are confident about its potential to effectively realize our hypothesis.

X. REFERENCES
1) K. Smith, P. Jaqueline. "Storytelling Companion - Personal Robots Group". Personal Robots Group MIT, 2016. [Accessed: 14- Nov-2016].
2) M. Dredge, T. Stuart. | "Children's Reading Shrinking Due To
Apps, Games And Youtube". The Guardian, 2013. | [Accessed: 14-
Nov- 2016].
3) Rowan, Cris. "The Impact Of Technology On The Developing Child". The Huffington Post, 2016. [Accessed: 14- Nov- 2016].
4) "Linear Book Scanner - The open-source automatic book scanner",
Linearbookscanner.org, | 2016. | [Online]. | Available:
https://linearbookscanner.org. [Accessed: 17- Nov- 2016].
5) J.Y. Lim, R. Snyder, “Linear Book Scanner”, Team 23, University of Michigan, Michigan, 2013. [Accessed: 17- Nov- 2016].
6) "Book scanner ScanRobot® 2.0 MDS - The automatic page turner
solution", | Treventus.com, | 2016. | [Online]. | Available:
http://www.treventus.com/automatic-book-scanner-scanrobot.html. [Accessed: 17- Nov- 2016].
7) P. Charlton, F. Johnson. "Mechanical System For Lifting And Turning Bound Pages". University of Ohio, 2015: [Accessed: 17-Nov- 2016].
8) T. Shinbrot, "Page flipper for book copying", US4663873, 2016.
9) E. Shemoul, "Page turner", US5373772, 1994.
10) A. Tillinghast, "Automated page turner", 20050230592, 2005.

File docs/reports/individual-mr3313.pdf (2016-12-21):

## Making PiNAOqio Read: Digitizing Text From Physical Books

Mihnea Rusu (mr3313)
Imperial College London

Abstract: Today’s families spend more time connected and less time together [1]. Parents, therefore, have less time available to read to their children. We aim to solve this problem with PiNAOqio, the robot that reads paper books to young ones.
Paper has been and will continue to be an essential part of modern society. Having our robot read from physical books is as challenging from an engineering perspective as it is advantageous and rewarding to the users. The problems of reading from an image will be tackled with a special illumination rig and optical character recognition software running in an embedded Linux system.
I. INTRODUCTION
N [2] we hypothesized that by having a storytelling robot, PiNAOqio, read books to children, information retention and user experience would be improved over traditional audiobooks. One may now argue that e-books should be the obvious candidate for our project. However, with traditional printed book sales on the rise [3], it offers convenience to the user of our robot to be able to pre-load their existing titles as well as know that future hardcopy volumes they purchase will be reverse compatible. Additionally, a wider selection is available to the reader in print, as opposed to digitally in the form of e-books or audiobooks due to the ubiquity of paper.
It is mentioned in [4] that physical books are unlikely to go out of print. The people interviewed mention factors like smell, weight, and the feel of turning pages as key reasons for their continued pursuit of printed material. Furthermore, paper is currently the go-to solution when it comes to learning e.g. in a classroom environment, due to the spatial markers books provide [5]. Seeking to read physical books as part of our project may enable children born in today’s increasingly digital environment to read more paper copies, become better learners and (re)discover the joys of physical books.
Arguably the most essential sub-system of PiNAOqio is that which reads books. This report will lay out the requirements and constraints we impose and are faced with in constructing this system. A brief explanation behind the reasoning behind each one will be provided and candidate hardware and software solutions will be explored. Finally, the results of preliminary testing will be briefly discussed and future work will be laid out.

II. REQUIREMENTS
The book reading sub-system of PiNAOqio needs to perform two broad tasks: turn the pages of a book (which will not be discussed in this report) and extract the text of the currently opened pages. We shall restrict our scope to only include printed books in English, as opposed to manuscripts or printed material in other languages.
In order to digitize a page into text, a photograph will be taken of that page and OCR will be applied. The reading system will be built separately from the NAO robot. We have decided this for two reasons: it’s required to perform computationally intensive tasks and it gives us more freedom with the entire concept of our robot.
In an ideal situation, our requirements would be as follows (in no particular order):
A. Text to be available to the speech synthesis system with unnoticeable latency from when the page-turning system reaches a rest state after flipping a page.
B. The throughput of words should be constant and in real-time, as PiNAOqio is speaking.
C. There should be no difference between the book and the spoken word i.e. text accuracy should be 100%.
With more development time and resources available (both hardware and financial) all of the above requirements are achievable, as will be explained below. As it stands though, a more realistic set of requirements would be to prioritize real-time throughput, allow a minimum level of noticeable latency and assume not all text will be fully accurate. Throughput would hide the high latency during reading. The increased latency would only pose a problem the first time the robot begins reading. Turning the page would be timed to begin from a specific time prior to the estimated current page’s ending time in order to eliminate the otherwise-apparent delay.
Furthermore, to prevent obvious text inaccuracies (e.g. non-alphanumeric symbols in the middle of a word) from being spoken, pre-determined placeholder actions can be performed by PiNAOqio such as coughing, sneezing, “uhm”-ing, etc. These will also enhance the human-like qualities of the robot.
There are a number of challenges associated with

I

achieving accurate OCR. Firstly, is the need for a high pixel-per-inch (PPI) count. A major use of OCR technology is in creating searchable text documents from scanned material. Images from a scanner are advantaged by a high PPI count due to the proximity of the scanner’s sensor array to the page. In our application, the page flipping mechanism needs a minimum clearance from the camera to operate. Additionally, we are limited by the focal length of the available lens and the requirement to capture an open book.
To obtain comparable OCR results to those obtained from a scanned page, our solution is to use a high resolution camera. Processing large image files however is a more intensive process and will increase the system’s latency further. To increase effective PPI, we could opt for a mobile camera axis that would capture the open pages section by section – the camera could be positioned at smaller height away from the page. This solution, while attractive, increases mechanical complexity and is simply unfeasible given the development time available.
A second challenge we are faced with in obtaining accurate OCR is that of adequate page illumination. Scanners achieve consistent illumination across the entire page by evenly illuminating only the area being scanned at the time – which is small; the page also lies perfectly flat inside. Our system requires even levels of illumination across a larger area – an open book - ideally without gradients, highlights or shadows.

III. HARDWARE
For the system’s hardware we are using a Raspberry Pi 3, together with a Raspberry Pi v2 camera which features an 8MP sensor and a maximum photo resolution of 3280x2464 pixels. We could have opted to use NAO’s built-in camera, but this was disadvantageous for three main reasons. First of all, its camera is of inferior quality to the one we are currently using. Secondly, because NAO would be forced to look at the book at an acute angle, a skewed image would be obtained. Deskewing algorithms are applied by OCR software as a standard feature, however this would lead to uneven text PPI across the page, and thus could potentially harm our text recognition performance.
Finally, the robot would be forced to look down at the book every time it needs to photograph an open page spread – which always occurs after a page flip. To the reader, this would look scheduled and unnatural after a number of pages. With a separate system, we have the freedom to do the action of looking down at the book more randomly and naturally in order to build the ‘believability’ of PiNAOqio to the human user.

Initial experimentation in creating adequate light for OCR involved using an LED ring light around the Raspberry Pi Camera. Due to the lack of optics on the diodes, the light was not directional and would cause camera glare. Moreover, the light output from a dozen LEDs in the ring did not provide sufficient illumination from our camera’s focus height.
Further thought revealed that the engineering challenge of evenly illuminating a large area with diffuse light has already been tackled. Liquid Crystal Display (LCD) backlights are ubiquitous and feature such technology. A backlight is typically constructed of several layers, as shown in Figure 1.

We obtained a backlight from a recycled LCD display. The backlight originally used CFL tubes as a source of light (denoted as (a) in Figure 1); these require a source of high voltage and as such would not be adequate for a prototype that is to be evaluated with people, especially children. To fix this issue, we replaced the source of light with white LED strips around the entire perimeter of the acrylic sheet (d). Downsizing the backlight was done by laser cutting the acrylic sheet to the dimensions required to fit inside the frame that was built to accommodate one book; a central hole was cut to allow the camera to peer through. Sealing the edge of the acrylic inside the hole was necessary to avoid camera glare and was achieved with opaque white tape (also to serve as a side reflector).

IV. SOFTWARE
The software component of the system can be broken down in three components: a) image acquisition; b) pre-processing; c) OCR. A software pipeline links all the components together; all scripts are designed to run on the

Figure 1: Side view of the LCD backlight layer stack-up. (a) are two Compact Fluorescent Lightbulb (CFL) tubes; (b) is a thin metallic frame that houses (a) and holds the entire stack-up; (c) is a sheet of white opaque plastic serving as a reflector; (d) is an acrylic plate with a honeycomb pattern etched on the side facing towards (c) to give it the properties of a diffuse light pipe; (e) and (g) are two diffuser sheets; (f) is a prism lens (also known as a brightness enhancing film or BEF for short) that focuses light akin to a Fresnel lens.

Raspberry Pi. In the eventuality that computational load should diminish user experience or there is sufficient time remaining for developing further enhancements, the intensive aspects of processing may be offloaded to more powerful machines in the cloud using technologies like Amazon Web Services (AWS). It is helpful in that regard that no additional hardware will be needed – the Raspberry Pi 3 has an on-board Wi-Fi radio. Lastly, it should be mentioned that our code is version controlled using GitHub, for good software engineering practice.
A. Image acquisition
To obtain images from the camera, the built-in Raspberry Pi Bash command raspistill is used. This command captures an image from the camera, with a provided set of exposure parameters i.e. shutter speed, ISO, exposure compensation, etc.; image quality and image size. A list of available output formats may be found in [6].
The raw format is useful for preserving all information from the sensor at the cost of increased memory usage and computation time further in the pipeline. Lossy compressive formats may be specified for boosting throughput and significantly reducing memory cost, but they are not without fault. According to [7] lossy formats that use the Discrete Cosine Transform (DCT) such as JPEG are to be avoided for photographing subjects featuring high spatial frequencies such as text. Ringing around sharp edges becomes visible with increased compression ratios. A proposed alternative to JPEG is JPEG2000, which uses the discrete wavelet transform (DWT) to ameliorate the problem of ringing, while keeping or even improving the memory cost and
throughput | benefits | of | JPEG. | Unfortunately,
raspistill does not provide the option of JPEG2000 compression and as a result we have decided to use lossless PNG compression as a trade-off between the two extremes.
B. Pre-processing
Following image acquisition, the raw image of the open book is processed before the OCR stage to make text recognition faster and more robust. Firstly, the position of the camera will remain constant and approximately so will the book’s (some movement may occur as the spine of the book shifts). We can use a divide and conquer approach to crop the single input image into a series of smaller sub-images. OCR can then be applied on each sub-image in sync with the requirements of NAO’s speech synthesis engine, reducing the page-flip-tospeaking latency and as a result the system’s start-up time from rest.

The challenge with this idea arises from sectioning text such that it doesn’t get cut off in any sub-image. Since the book location is only approximately constant, we cannot assume that all lines of text will be in the same location across subsequent input images.
Secondly, the pre-processing stage should apply image enhancement filters for bettering OCR performance. Such enhancements have been shown in [8] to boost the performance of open-source OCR software to commercial standards. We have determined empirically that increasing contrast, brightness and black levels, as well as converting the image to greyscale has a positive effect on the resulting text accuracy. Under the assumption that the pages’ surface is evenly lit, the previous statement is true; otherwise in some cases it may provide worse results than without image enhancements. For our prototype, the actual filter parameters would need to be tweaked before the demonstration, to accommodate the lighting conditions of the surrounding environment. Despite having the backlight panel as a fixed artificial source of diffuse light, its power output is not enough to overpower that of the sun’s, for example, on a clear day.
All our pre-processing algorithms are performed using a combination of OpenCV in Python and command-line programs including Textcleaner (as in [8]).
C. Optical Character Recognition
The final stage of the pipeline is converting the image (or sub-image) with all its applied enhancements into text. There are numerous OCR packages available for Linux. Despite that, only a small number of open-source OCR engines are employed by the majority of these packages. Other proprietary engines for which one must pay a licensing fee for usage permission do exist, though they do not fit within our target budget.
An analysis shown in [9] compares the accuracy of 5 common optical character recognition engines: ABBYY, Cuneiform, GOCR, Ocrad and Tesseract; the first being the only closed-source one on the list. As one would expect, the proprietary software from ABBYY scored the highest – 100% accuracy, but also took on average approximately 5 times longer than the second slowest (Tesseract) to return an answer. A further evaluation of engines ABBYY, Tesseract and the open-source OCRopus in [10] draws a similar conclusion – proprietary OCR engine ABBYY is the superior software available on the market, but Tesseract is the best open-source alternative. Finally, a comparison between ABBYY and Tesseract in [11] concludes that both engines have their merits and demonstrates that there are areas where Tesseract outperforms ABBYY in accuracy, such as when fonts contain glyphs. It is apparent that Tesseract is likely the best performing open-source engine.
We have decided to choose Tesseract as the backbone of our reading system. The software benefits from being actively maintained and updated by the community as well as from the ability to easily train its classification stage using arbitrary fonts and languages. Furthermore, over 100 languages are supported by Tesseract without any further training, enabling us to expand the scope of our requirements with ease.
V. EVALUATION
Initial testing of our system using Tesseract, prior to installing the updated backlight panel illumination solution provided hopeful results. High contrast, clear text on the pre-processed image resulted in 100% accurate OCR, whereas dimly or unevenly lit areas were not at all correct. While the final stage of the software pipeline is slow indeed, it is not slower than the time for a human to orate the open pages at a normal rate. This is favorable as it will manage to keep up with a throughput as per our requirements, while also providing us ample time for the page turning action.
The latency from when a page is flipped to when the pages have been read is high, however, as mentioned in the requirements section, this is only a problem when the reading pipeline begins from rest or from an invalid state (i.e. user has forcefully flipped the page). After the pipeline has been initialized, the latency becomes masked by the throughput of text – the only visible observation will be that what the robot is reading may not necessarily be what the book’s currently open pages read.
Our conclusion from the preliminary tests was that lighting plays a more important role in optical character recognition than we initially anticipated. It is the reason we sought to find an adequate source of illumination i.e. the backlight panel.

VI. FUTURE WORK
A bright source of diffuse light shining upon a book may lead to good OCR, but could be considered a distraction by the user. An alternative pursuit of adequate illumination could involve building our bespoke backlight panel for infrared (IR) wavelengths and using the IR version of the Raspberry Pi camera instead of the current one. This would make the panel less obtrusive to the user. Work still needs to be done in linking all components of our system together and getting their output to NAO. This will be done over the Ethernet connection that links the Raspberry Pi to the robot by means of standard networking packets. Finally, the book reading software subsystem will require the introduction of additional logic to enable high-level communication with the speech synthesis engine in the NAO robot.

VII. CONCLUSION
In conclusion, making NAO read printed books with an embedded system is no mean feat. There are several challenges in achieving this while keeping the robot human friendly, which include computational expense and the need to create special lighting conditions. We mask the latency induced by the former with a sufficient level of throughput and we tackle the latter with a rig made from a recycled LCD backlight. While further work is necessary before PiNAOqio is literate, initial experimentation showed that our aim is achievable.

VIII. BIBLIOGRAPHY

[1] J. Elgot, "One In Five See Family For 'Less Than An Hour A Day'," The Huffington Post, 1 April 2015.
[2] X. L. Soler, P. Korkontzelos, N. Warner and M. Rusu, "PiNAOqio: Storytelling for children using physical books and HRI," 2016.
[3] M. Sweney, "Printed book sales rise for first time in four years as ebooks decline," The Guardian, 13 May 2016.
[4] J. Catone, "Why Printed Books Will Never Die," Mashable UK, 16 January 2013.
[5] C. Myrberg and N. Wiberg, "Screen vs. paper: what is the difference for reading and learning?," Insights, vol. 28, no. 2, pp. 49-54, 2015.
[6] Raspberry Pi Foundation, "Camera Module v2 Documentation," [Online]. Available:
https://www.raspberrypi.org/documentation/hardware/camera/README.md. [Accessed 16 November 2016].
[7] T. Ebrahimi and M. Kunt, "Visual Data Compression for Multimedia Applications," in Proceedings of the IEEE, 1998.
[8] vBridge, "How we tuned Tesseract to perform as well as a commercial OCR
package," | 5 | November | 2012. | [Online]. | Available:
http://vbridge.co.uk/2012/11/05/how-we-tuned-tesseract-to-perform-as-wellas-a-commercial-ocr-package/. [Accessed 16 November 2016].
[9] A. Gohr, "Linux OCR Software Comparison," 15 June 2010. [Online].
Available: | https://www.splitbrain.org/blog/2010-06/15-
linux_ocr_software_comparison. [Accessed 16 November 2016].
[10] U. Springmann, "Other OCR engines: ABBYY, Tesseract," Ludwig-Maximilians-Universität München (LMU), 14 September 2015. [Online]. Available: http://www.cis.lmu.de/ocrworkshop/data/slides/m6-abbyytesseract.pdf. [Accessed 16 November 2016].
[11] M. Heliński, M. Kmieciak and T. Parkoła, "Report on the comparison of Tesseract and ABBYY FineReader OCR engines," PCSS, 2012.
[12] H. Furness, "Books are back: Printed book sales rise for first time in four years as ebooks suffer decline," The Telegraph, 13 May 2016.

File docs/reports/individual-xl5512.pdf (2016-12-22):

# Speech

# Processing Component

# Report for PiNAOqio

## Xavier

Laguarta (xl5512@ic.ac.uk)

Abstract -‐ In

order

to

test the hypothesis set

in

our
previous

design

report, our

robot

must

be

able

to

hold
a

conversation

(speech

recognition)

and

read

a
physical

book (text

to

speech).

Here

we

will give

a
brief

background

on

both

the

speech

recognition

and
text

to

speech

technologies

as

well

as outline

the
importance

of

having

a

natural human

robot
interactive

system.

Next,

a

more

in

depth

study

of

both
speech

recognition

and

text

to

speech

technologies
will

take

place,

followed

by

a

comparison

of

different
tools

available.

Finally

the current implementation and

the

remaining

steps will

be

discussed.
I.

INTRODUCTION

A

very

important

requirement to

prove
our

initial hypothesis defined

on

the

previous
Design

Report

is

for our

robot

to

have

a

natural
interaction with

humans.

This

report

will

focus
on

the

speech

interaction,

which

will

take

place
through

our

spoken

dialog

system,

comprising
of

both

a

speech

recognition

system

and

a

text
to

speech

system [1].

The

overall

system

will
involve an initial

conversation between

the
human

user

and

the

robot,

followed

by

the
reading

action

and

further

interaction
throughout

the

reading.

Some

requirements
have

been

set

in

order

for

our

system

to

be
robust

and

available

to

any

user,

instead

of
trained

for

one

specific

user [2].

These involve
having

a

short

domain

of

words

to

be
recognised,

as

well

as

a good

quality

headset
microphones

to

eliminate

as

much
environmental

noise

as

possible.

Initially,

some
background

knowledge

on

spoken

dialog
systems

will

be

set,

before

moving

to

the
human-‐robot

interaction

section.

Following,

an
overview

of

speech

processing

technology,

the
tools

considered

and

the

main

difficulties

will
be

specified.

Finally,

text

to

speech

technology
tools

and

the

current

implementation

will

be
outlined.

II.

BACKGROUND

Spoken

dialog

systems constitute of
several

components

that

will

be

described
further

in

the

report.

First,

we

have

an

automatic

speech

recognizer

(ASR)

system,
with

the

function

of

decoding

speech

into

text.
Next,

a

dialog

manager and

domain

reasoner
will

be

in

charge

of

the

flow

of

conversation
between

the

robot

and

the

user [3].

More
specifically,

this

will

decide

what

actions

must
be

taken

depending

on

the

words

spoken

and
what

should

be

answered.

Although

some
dialog

managers

incorporate

ways

to

clarify
misunderstandings

in

the

conversation,

we

will
not

be

implementing

such

a

complex

system
due

to

the

time

constraints

of

the

project [4].
Finally

the

text

to

speech

(TTS)

system

will,

as
its

name

infers,

transform

utterances

into
speech.

Several

ASR

and

TTS

systems

will

be
compared.

III.

HUMAN-‐ROBOT

INTERACTION

(HRI)

The initial conversation

between

the
human

and

the

robot prior

to

the

reading can
be

seen

in

figure

1:

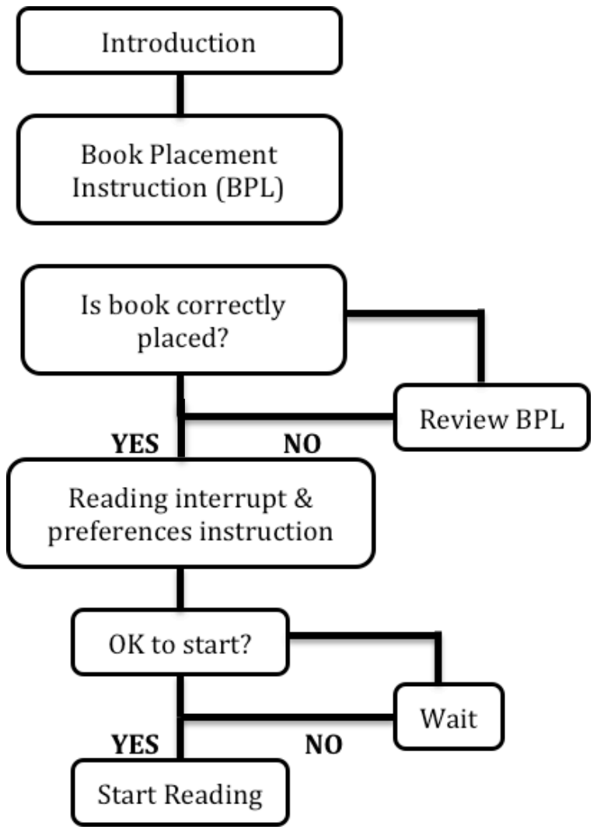
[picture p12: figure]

Figure

1:

Human

robot

interaction

prior

to

reading

Above

we

can

observe,

the

speech

interaction

is
kept

at

a

minimal

level to

allow

for

a

minimum

number

of

words

in

our dictionary.

As
explained

further

on,

this

will

give a

higher
accuracy

for

the speech

recognition system
while

keeping

it

user-‐independent.

The

initial
introduction

will

comprise

of

basic

salutations
and

instructions

as

to

how

to

position

the

book
on

the

page

turning

mechanism.

Following,

a
couple

questions

referring

the

user’s reading
preferences will

be

asked and

instructions as

to
how the

user should

interrupt

the

reading

in
the

case

they should

desire

it will

be

stated.
Finally,

while the

robot

reads

the

passage,

it

will
be

listening

to

any

instructions

coming

from

the
user.

We

are

targeting kids

in

the

ages
ranging

from

4-‐12

years

of

age,

meaning

we
must

focus

on

having

a

simple

and

robust
system.

For

the

best

possible

user

experience,
our

system

should be

capable

of listening

to

the
user’s

commands

and

appropriately

answer

to
them.

When

looking

at

the

important

of
communication,

several

parameters

can

be
analysed

for

a

better

HRI.

These

include

both
verbal

and

para-‐verbal

parameters.

We

identify
verbal

parameters

as

the

expressions

used

and
para-‐verbal

parameters

as

the

characteristics

of
speech,

including

the

speed

and

the

volume

[5].
Due

to

the

complexity

of

the

verbal

parameters
and

the

scope

of

the

project,

only

the

para-‐
verbal

parameters

will

be

considered.

The

overall

speech

system

will
communicate

through

an

Ethernet connection.
More

specifically,

an

Ethernet

cable

will

be

used
to

connect

the

raspberrypi,

where

the

computer
vision

and

page

turning

mechanisms

will

be
running,

with

the

NAO

robot.

The

whole

spoken
dialog

system

and

NAO

movement

will

be

run
on

the

NAOqi

operating

system.

Furthermore,
the

dialog

manager

will

be

created

in

python.
The

purpose

of

a

dialog

manager

is

to

follow

the
current

state

of

interaction

and

combine

this
with

the

user

inputs

to

give

an

appropriate
action,

which

would

be

the

next state [6].

IV.

SPEECH

PROCESSING

Speech

coming

from

kids

is

very
different

than that

from adults,

and

not

only

in
frequency.

We

must

therefore

develop

a

very
robust

spoken

input

system. As all

things
coming

from

our

environment,

information

has

to

be

digitalised

in

order

to

be processed.

In

the
case

of

speech,

we

are

sampling

and

quantising
air

pressure.

Once

in

the

form

of

an

audio
stream,

there

is

a

lot

of

information

we

can
obtain,

varying

form

linguistic

information,
prosodic

information

(emotional) and

identity
information

[7].

Focusing

on

linguistic

information,

an
Automatic

Speech

Recognition

(ASR)

system

is
used,

along

with

voice decoder

software.

The
decoder

is

comprised

of

two

sections,

the
language

model

and

the

acoustics

model.
Firstly,

the

acoustic

model

contains sounds

we
call

phonemes,

which make

up

a

language.
These

are

sounds

that

we

say

when

phrasing
words

or

sentences,

and

are

written

exactly

as
they

sound.

A

statistical

speech

recogniser,
which

uses

a

Hidden

Markov

Model

(HMM) [8],
can

determine

the

likelihoods

of

those

acoustic
observations.

A

finite-‐grammar

or

statistical
language

model

can

construct

a

space

where
HMMs

are

built

by

the

acoustic

model.

Secondly,
the

language

model

is

divided

into

word
lexicon,

the

database

of

words

to be

recognised
by

the

ASR

system,

and

grammar,

containing
the

sets

of

words

that

follow

the

grammar

rules.
These

will

link

each

sequence

of

phoneme

to
words.

The

grammar

will

consist

of

predefined
links

between

words

and

how

likely

each

link

is.
The

language

model

however

will

statistically
tell

us

how

likely

it

is

for

a

word

to

follow

the
previous

word

thanks

to

the

frequency

of

such
followings.

N-‐Grams

tells

us

the

N-‐1

preceding
words

that

can

arise.

Tri-‐grams

and

bi-‐grams
are

most

often

used

as

these

require

less
training

than

higher

order

N-‐grams

and

are
therefore

more

often

used [9].

Furthermore,

there

are

two

methods
that

can

be

used

to

improve

the

accuracy

rate of
a

system:

training

an

acoustic

model

for

a
specific

user

or

having

a

small

vocabulary

of
words

from

which

to

chose

from.

We

have
decided

to

keep

our

vocabulary

of

words

small
in

order

to

keep

our

model

flexible

for

any

user.

V.

SPEECH

PROCESSING

TOOLS

Although

the

NAO

comes

with

a

default
speech

recognition

tool

from

NUANCE [10],

we
will

be

using

pocketsphinx

for

this

project
because

of

its

local

use (offline),

being

open

source, and its

adaptability

to

robots

with
relatively

small

computing

power,

as

well

as

a
better

accuracy

when

compared

to

the

default
tool.

With

pocketsphinx

we

find

an acoustic-‐
model

called

Hub4,

as

well

as

a

language

model
that

can

be adapted

for any

speaker [11].

Due
to

the

time

frame

of

this

project and

the

goal

of
interacting

with

several

people

at

a

time,
training

for

specific

speakers

will

not

take
place,

although this

would

increase

the
accuracy

rate.

When

deciding

between

pocketsphinx
and

other

tools

with

better

performance,

such
as

Google

Speech

or

Nexiwave [12], our

choice
was

based

on

the

tools

being

local

instead

of
being

distributed.

Not

only

do

distributed tools
drain

more

battery,

they

also

have

a

delay

of
about

three

seconds,

which

was

not

desired

for
our

system.

Instead

we

decided

to

keep

our
system

local

and

design

it

to

a

more

basic
standard.

Other

tools

that

also

proved

better
performance,

such

as

Julius or

Kaldi,

were
discarded

due

to

the

complexity

of

their
documentation

and

the

extensive

knowledge
needed

to

operate [13]. Finally,

NUANCE’s

best
selling

software

tool

called

Dragon

seems

to
provide

very

high

accuracy,

although

this

tool
must

run

on

machines

much

more

powerful
than

a

rasberrypi,

let

alone

the

NAO

robot.

VI.

ENVIRONEMT

NOISE

One

of

the

main

issues

with

speech
recognition

is

the

noise

coming

from

the
environment.

This

noise

will

deteriorate

the
quality

of

the signal

being

inputted

into

our

ASR
and

therefore

decrease

the

accuracy

of

our
system.

Several

methods

can

be

used

to

surpass
this

complication.

Studies

show

that

one

of

the
most

important

factors in

speech

recognition

is
the

microphone [14].

As

the

microphone

built
into

the

NAO

works

at

an

unacceptable

level
and

our

robot

is

intended

to

read

in

a

fixed
position,

microphones

can

be

position
wherever

we

find

them

most

desirable to
improve

the

quality

of

the

signal. The

best
method

of

receiving

a clean signal

is

through

a
headset,

which the

user

will

speak

into

directly
[15]. The

short

distance

between

the

user’s
mouth

and

the

headset

microphone

will

allow
for

a

very

small

amount

of

noise

to

be

added

to
the

signal.

Although

headset

is

the

best

option,

desktop

microphones

can

also

work

well if

its
distance

to

the

user

is

kept

low.

VII.

TEXT

TO

SPEECH

Speech

synthesis

allows

for

the
formulation

of

human

speech

from

a

text

string.
In

PiNAOqio’s

case,

this

would

be

used

during
the

initial

introduction

with

the

user,

and

most
of

all

while

reading

the

book.

Here,

strings

will
be

passed

from

the

computer

vision

system

and
synthesised

into

speech [16].

In

order

to

create
these

sounds,

a

system

will

have

a

database

that
stores

either

words

or

phones

and

diphones.
The

latter

will

allow

for

a

more flexible

system,
although

the

words

will

not

be

as

clear [17].
Festival

Speech

Synthesis

System

is

an

example
of

a

diphones

based

synthesis

tool

[18].
However,

new

tools

have

been

developed

that
allow

for

a

clearer

sound.

When

choosing

the

most

appropriate
text

to

speech

tool,

Api.ai

and

IBM’s

Watson
were

the

most

powerful

tools considered. These
tools

allow for

more

flexibility when

passing
text

to

speech, allowing

us

to

experiment

with
para-‐verbal

manipulations

mentioned

earlier
[19].

More

specifically

they

allow for
expression of

emotions

through

voice

or the
expression

of a

childlike

voice.

However,

due

to
the

time

constraint

on

our

project,

and

the
complexity

of

the

speech

recognition

section,
Aldebaran’s

default

text

to

speech

tool

will

be
used. Aldebaran

uses

NUANCE’s

text-‐to-‐speech
technology,

where

some

customization

of

the
voice

can

also

be

accomplished:

the

speed,

pitch
and

echo

of

the

speech

can

be

pre-‐defined [20].

VIII.

IMPLEMENTATION

Using

pocketsphinx

as

the

speech
recognition tool

and

open

source

code from
GitHub,

I

have

started

to

record

sounds

that

are
then

to

be

repeated

back

to

me.

This

has

been

a
good

way

to

evaluate

the

most

basic

features

of
pocketsphinx.

Furthermore,

in

order

to
evaluate

the

improvement

from

personalized
speech

recognition,

I

have

done

research

as

to
how

to

create

a

personalized

acoustic

model.
Next,

the

initial

conversation

system

will

be
built,

where

the

conversation

will

be

guided

to
the

desired

direction

and

the

reading

will

begin
once

the

book

is

well

placed.

Finally,
Aldebaran’s

text

to

speech

tool

allows

for

an

easy

implementation

of

string

to

speech.
Although

individual

strings

have

been

tested,
the

next

step

will

be

testing

this

tool

with
strings

coming

from

rasberrypi’s

computer
vision.

IX.

CONCLUSION

Speech

processing

is

one

of

the

main
points

to

consider

for

PiNAOqio’s user
experience

while

reading,

and

hence

an
important

point

in

our

hypothesis.

Although
spoken dialog

systems

are

constantly
ameliorating
| and

can

be

customised

to

great
extents, | for the

purpose

of

this project

the
potential | of speech

recognition

and

text

to
speech | tools have

been

kept

to

a

basic

level.

The
implemented
| system

will

allow

PiNAOqio

to
have

a

basic

| initial

conversation

and

read

while
still

allowing

| further

input

from

the

user.
Although | the implementation

is

currently

at

an
initial | stage, the

results

of

the

most

basic
version | have been

positive.

REFERENCES

[1]

T.

Kanda, | M. Shiomi,

Z.

Miyashita,

H.

Ishiguro,

and

N.
Hagita,
“A | communication

robot

in

a

shopping

mall,”

IEEE
Robotics | and Automation

Society,

vol.

26,

no.

5,

pp.

897–
913,

2010.

[2]

M.

A. | Goodrich and

A.

C.

Schultz,

“Human-‐robot
interaction: | a survey,”

Foundations

and

Trends

in

Human-‐
Computer | Interaction,
vol.

1,

no.

3,

| pp. 203–275,

2007.

[3]

McTear, | M. F.,
| 2004.

“Spoken

Dialogue

Technology:
Toward
the | conversational

user

interface”,

1st

ed.
Springer, | pp. 323-‐324.

[4]

Shriberg, | Elizabeth,

(2004):

"Direct

modeling

of
prosody:

an

| overview

of

applications

in

automatic

speech
processing", | In SP-‐2004,

pp.

575-‐582

[5]

Z.

M.

Hanafiah,

C. Yamazaki,

A.

Nakamura,

and

Y.

Kuno,
“Human-‐ robot
| speech

interface

understanding

inexplicit
utterances | using vision,”

in

CHI’04

extended

abstracts

on
Human

factors

| in computing

systems.

ACM,

2004,

pp.
1321–1324.

[6]

Kozima, | H., Nakagawa

C.,

and

Yasuda,

Y,

“Interactive
robots
for | communication-‐care:

A

case-‐study

in

autism
therapy”, | 2005, pp. 341-‐346,

2005.

[7]

S.

Fujie, | Y. Ejiri, Y.

Matsusaka,

H.

Kikuchi,

and

T.
Kobayashi, | “Recognition

of

paralinguistic

information

and
its

application

| to spoken

dialogue

system,”

IEEE
Workshop | on Automatic

Speech

Recognition

and
Understanding
| (ASRU

’03),

pp.

231-‐236,

2003.

[8]

M.

Gerosa,

D.

Giuliani,

S.

S.

Narayanan,

and

A.

Potami-‐
anos,

“A

review

of

asr

technologies

for

childrens

speech,”
Proc.

WOCCI’09,

2001,

vol.

49,

pp.

847–860.

[9]

D.

Jurafsky

and

J.

H.

Martin,

“Speech

and

Language
Processing:

An

Introduction

to

Natural

Language
Processing,

Computational

Linguistics,

and

Speech
Recognition”,

2nd

ed.

Prentice

Hall,

2009.

[10]

ALSpeechRecognition

— Aldebaran

2.1.4.13
documentation.

2016.

(Available

at:
http://doc.aldebaran.com/2-‐1/naoqi/audio/alspeechrecognition.html.)

[11]

D.

Huggins-‐Daines,

“Pocketsphinx:

A

free,

real-‐time
continuous

speech

recognition

system

for

hand-‐held
devices,”

in

Proceedings

of

the

IEEE

International
Conference

on

Acoustics,

Speech

and

Signal

Processing,
2006.

(ICASSP

2006).

Toulouse,

France:

IEEE

Xplore,

May
2006.

[12]

Lange,

P.,

Suendermann-‐Oeft,

D.:

Tuning

Sphinx

to
outperform

Google’s

speech

API.

In:

Proc.

of

the

ESSV.
(2014)
[13] Lee,

A.,

Kawahara,

T.,

&

Shikano,

K.

(2001).

Julius-‐An
open

source

real-‐time

large

vocabulary

recognition
engine.

NAISTAR.

[14]

Y.

Sasaki,

S.

Kagami,

H.

Mizoguchi,

and

T.

Enomoto,

“A
predefined

command

recognition

system

using

a

ceiling
microphone

array

in

noisy

housing

environments,”

in
Proceedings

of

the

2008

IEEE/RSJ. Nice,

France:

IEEE
Xplore,

Sep.

2008,

pp.

2178–2184.

[15]

W.

Khaewratana,

“Development

of

a

Voice-‐Controlled
Human-‐ Robot

Interface,”

Thesis,

RIT

Scholar

Works.NY,
5th March

2016.

[16]

Taylor,

Paul

(2009).

Text-‐to-‐speech

synthesis.
Cambridge,

UK:

Cambridge

University

Press.

[17]

Allen,

Jonathan;

Hunnicutt,

M.

Sharon;

Klatt,

Dennis
(1987).

From

Text

to

Speech:

The

MITalk

system.
Cambridge

University

Press.

[18]

W.

Black

and

K

Lenzo.

2007.

Festvox:

Building

syn-‐
thetic

voices,

Version

2.1.

http://www.festvox.org/bsv/.

[19]

Imai,

T.

Kobayashi,

K.

Tokuda,

T.

Masuko,

K.

Koishida,
S.

Sako,

and

H.

Zen.

2009.

Speech

signal

processing

toolkit
(SPTK),

Version

3.3.

http://sp-‐tk.sourceforge.net.

[20] Nuance.com.

2013.

Aldebaran

Robotics

and

Nuance
Revolutionize

Human

– Machine

Interaction.
http://www.nuance.com/company/news-‐room/press-‐releases/Aldebaran_web.docx.

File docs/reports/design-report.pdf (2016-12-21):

## PiNAOqio: Story-telling for children using physical books and HRI

Xavier Laguarta Soler (xl5512), Periklis Korkontzelos (pk1913), Nathan Warner (njw13), Mihnea Rusu (mr3313) Imperial College London

Abstract: Recent advances in technology have led to
a decrease in the reading of physical books in children [1]. Overuse of modern devices (e.g. smartphones, tablets) from an early age poses long-term health risks [2].

Our aim is to combine the old and the new; physical books with human-robot interaction (HRI) as a novel form of entertainment and education. We propose using a friendly miniature humanoid robot in conjunction with a page-turning mechanism to read books and interact with children. The system shall be evaluated through measurement of the level of information retention and user experience across different levels of HRI.

I. INTRODUCTION

In circumstances where a human story teller is not available the only alternative for small children would be an audio book. Due to the absence of interaction and human qualities audio books are not well received by children with limited attention spans. PiNAOqio offers to resolve this issue by actively engaging and interacting with the audience; both through advanced humanoid gesticulations and verbalized feedback related to the text. The ability of PiNAOqio to turn the pages of a physical book retains the feel of “real” books that is lost when they are digitized, and also allows users to load their own pre-existing volumes.

PiNAOqio will be versatile enough to be deployed in a range of situations and environments. In particular children that have to be hospitalized for long periods of time experience stress and anxiety [3] and would benefit, having their day-to-day routines greatly enhanced by hearing some of their favorite stories. In no way does PiNAOqio intend to supplant genuine human interaction; it will however serve to make story reading a more fun and social experience for young listeners.

II. HYPOTHESIS

The aim of this project is to investigate the effectiveness of a “storyteller robot” as a source of engagement and educational entertainment for kids. The parameters measured will include user experience and the ability to retain information, upon which the following hypotheses are assessed. These figures have been arbitrarily selected to indicate satisfactory performance:

a) Story-telling by PiNAOqio will improve information retention and user experience by 15% and 30% respectively in comparison with story-telling by an audiobook.
b) Allowing the user to interrupt and interact with the robot, as well as make gestures to emulate a human story-teller, will improve the retention of information and the user experience by 10% and 20% respectively.

III. RELATED WORK

The challenge of designing an interactive robot that reads stories whilst engaging with its users has been tackled in the past. There are several existing robots that focus on either the user experience or the learning aspect of the interaction. For instance, the Storytelling Companion is designed by the Personal Robots Group by MIT [4] as a social character, relating to children as a peer, not as a teacher. Through a storytelling game that the robot and child would play together on a tablet, the aim was to improve language and vocabulary skills early on to help them succeed in the future. Another example is TROBO – the Storytelling Robot [5], which is a plushy robot that connects with an iPad or iPhone to read a digital storybook. Trobo has been designed to improve the user experience by forming an emotional connection with the robot and the story.

Both of the above examples are dependent on tablets to function – devices that children may also associate with other activities such as playing games or watching videos. Usage of tablets for a storytelling robot do not contribute to solving the problem of long-term overuse. Furthermore, none of the mentioned robots use physical pages – as a result, there is no encouragement for the children to read more physical books.
IV. HUMAN-ROBOT INTERACTION (HRI)

The interaction between the robot and the user has a key role in realizing the hypotheses set above. Given the target audience of young children, the PiNAOqio is designed to be simple yet highly interactive. The operation of the robot is illustrated in the flowchart shown in figure 1.

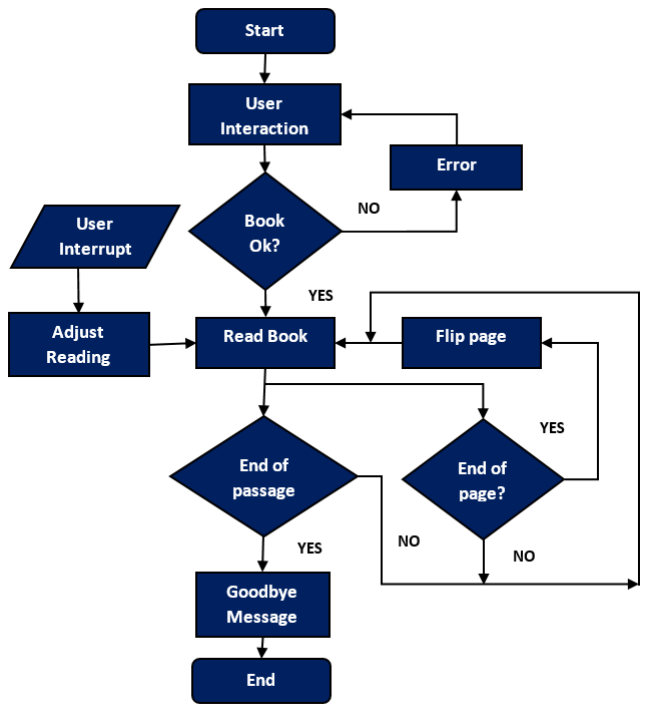
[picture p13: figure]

Figure 1: HRI operation flowchart Initially, there is a short conversation between the robot and the user which acts as an introduction. The aim is to familiarize the user with the robot and its functionalities and perform the loading of the chosen book. If the book has not been appropriately positioned, the robot asks the user to refit it. Once the book is correctly placed, the story begins. In tests where interaction is allowed, the user can interrupt the robot at any time using an external microphone. The user can then instruct the robot to adjust the reading profile to match his preferences by changing the reading speed and tone of voice.

Whilst reading, the robot checks to detect when the end of a page has been reached in order to activate the page flipping mechanism. The page flipping occurs simultaneously as the previous page is being read in order to reduce dead time. Once the entire allocated passage has been completed, the robot will again enter into conversation with the user. The aim is to thank the user for participating in the experiment and give them information about the questionnaires that will be used to assess the retention of information and user experience.

V. HARDWARE

The component to automatically flip the pages of a physical book will necessarily be mechanical and could be approached in a number of ways. Some existing systems accomplish this function using a weak vacuum with enough suction force to lift a page[6]; this can work well and poses little risk of damaging the book, however it is dependent on the suction making good contact with the page. Another approach involves raising a page slightly and using a burst of pressurized air to blow it over[7]; although this method can act the fastest, it is best suited to larger books with heavier pages. Finally, there are many varied systems that use a combination of servos and stepper motors to attain the same end[8][9]. We decided to opt with this latter option as we believed it to be the simplest to construct and also boasts the most reliable operation.

For this implementation to work there are several difficulties that need to be overcome. Firstly, unlike larger textbook types, with small fiction books the pages do not naturally fall to either side. As a result, the mechanism must be able to hold pages in place whilst also allowing for turning. This will require a “holding” servo on either side, where the servo arm can hold down the pages and also move up to catch a new page. Secondly, the curvature of the open book reduces performance of the OCR algorithm. To overcome this a small pressure will need to be applied to hold the book flat. The holding servos should be capable of multifunctioning to achieve this purpose. Finally, throughout the progression of the book the height of front and rear covers will vary. This requires each cover to rest on an independent platform. To deal with this either a stepper motor can control the height of each platform, or each platform can rest on springs where the weight of each side respectively determines height. In figures 2a and 2b below, we can see the page turning

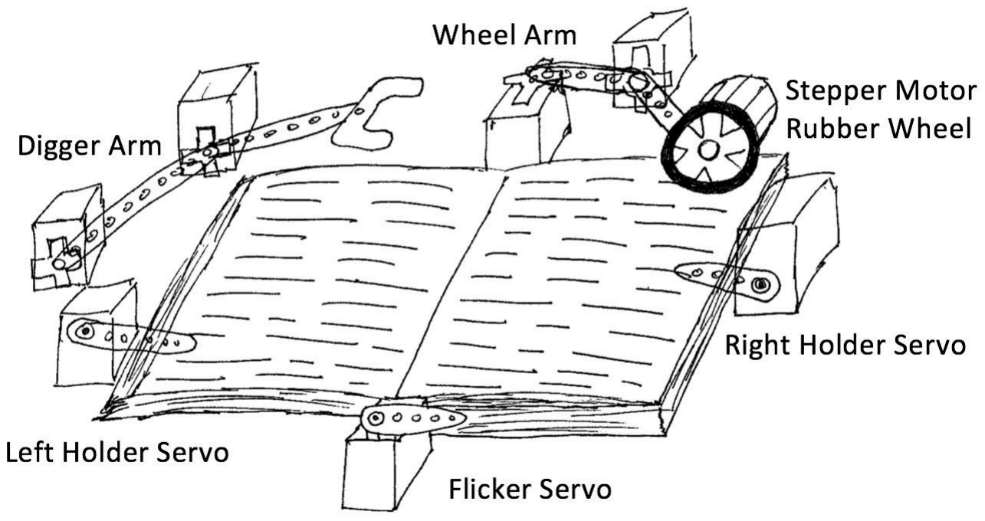
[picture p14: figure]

mechanism and the sequence of operation respectively.

Figure 2a: Page turning mechanism

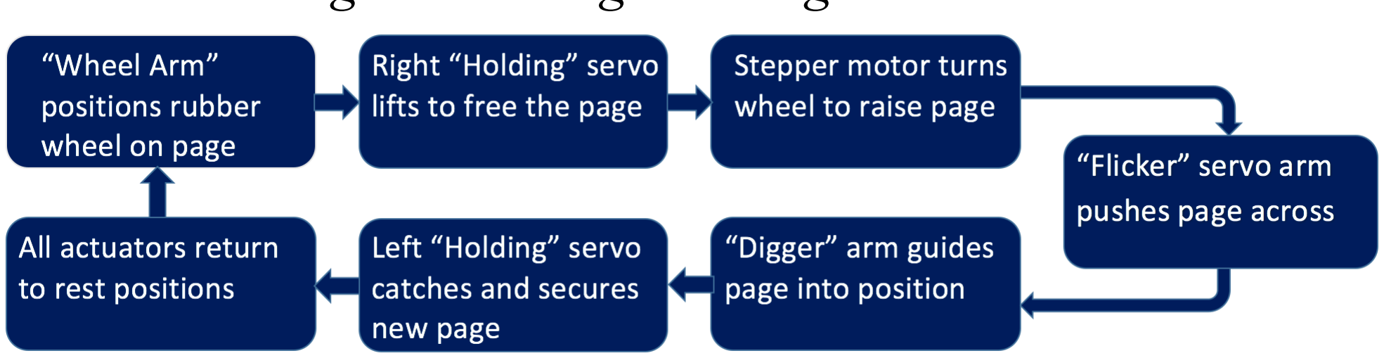
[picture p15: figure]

Figure 2b: Sequence of operation

Speech
Processing

Human-Robot
Interaction

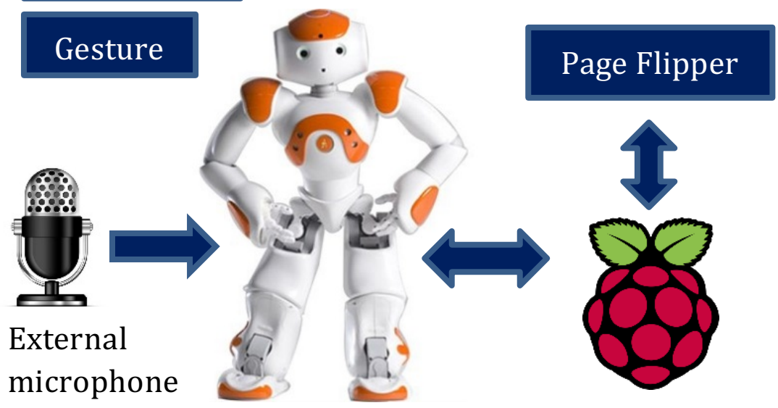
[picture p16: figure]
Gesture; Page Flipper; External microphone

NAO robot
Raspberry Pi 3

VI. SOFTWARE

We consider the following main software subsystems in our project: the page flipper mechanism, the camera, the gesture movement and the speech. The page turner and camera will be controlled by a Raspberry Pi 3; where as the movement and speech will be controlled by the robot (NAO) hardware. Nao will be using the NAOqi library
[10] to communicate with the Raspberry Pi over a wired network connection, which is available on the robot. A server-client model will be employed to facilitate the passage of information between the two subsystems. The Raspberry Pi will behave as a server, waiting for polls from the client (NAO). One advantage of the client-server model in this case is that it gives the client freedom to add extraneous HRI without knowledge of the lower level of the server. The system level of the software operations can be seen in figure 3.
A) Page Turner

A minimum set of high level operations, accessible through NAOqi by a custom API will be implemented in the prototype. Further functionalities may later be added. We assume for the time being that turning a page backwards is redundant for the purpose of simplicity in hardware design. The Raspberry Pi will be responsible for the low-level implementation of each of these functions: Start/Stop/Pause reading and turn page to next.

B) Camera

To ‘read’ a page, a camera will be used on the Pi to take a picture of the book. Image enhancements will be applied using OpenCV [11] in order to enable robust optical character recognition (OCR) using Tesseract-OCR [12]. Experiments will be performed to determine optimal camera placement and exposure using an artificial source of light which will be present on the final system as well. When a page needs to be flipped, a state machine will sequence the servos as per Figure 2b.

C) Gesture Movement

To enhance the interaction between robot and human, PiNAOqio’s motion capabilities are being exploited to provide a natural movement that imitates a human storyteller. NAO’s electric motors and actuators are designed and built to allow for 25 degrees of freedom (DOF), which is enough to emulate human gestures. Utilising existing APIs can significantly reduce design and testing time while also improving the user
experience. | An | example | includes | the
ALAutonomousMoves API which enables expressive listening through which the NAO makes a slight movement to show that it is listening. A further enhancement will be adding gestures that trigger on specific keywords.
D) Speech

Along with movement gestures, speech processing is an important tool for human-robot interaction. Apart from reading out the text from the chosen passage, speech recognition will be crucial for the initial interaction with the user. These functions will be split between the two following NAOqi APIs: the ALSpeechRecognition API, which translates spoken words to text, and ALTextToSpeech API, which translates words to speech. The speech recognition will run directly from the NAO as its internal computing resources are sufficient for our purposes. Due to the general complexity of our other hardware and software mechanisms no external speech recognition mechanisms will be used, such as PocketSphinx [13] or Apple’s Siri.

Figure 3: System level view of PiNAOqio
VII. EXPERIMENT

In order to evaluate our hypothesis several tests will be executed. Our experiments will have the objective of evaluating the level of text comprehension of the listeners as well as user experience for different tests: an audiobook, an HRI-deficient robot, and finally PiNAOqio with both gestures and full human-robot interaction functionalities, such as asking for user feedback in real-time or determining passage context.
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

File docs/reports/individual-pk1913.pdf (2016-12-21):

# Designing the Human-Robot Interaction for PiNAOqio

Periklis Korkontzelos (pk1913), Imperial College London

Abstract

This report consists of an overview of the Human-Robot Interaction (HRI) between the user and PiNAOqio, an educational robotic companion with the ability to read hard-copy books. The expected and desired outcomes from the HRI include the improvement of information retention and user experience, as an effect of increased interaction. PiNAOqio is designed to perform gestures that enrich the learning process and to emulate human storytellers in order to
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

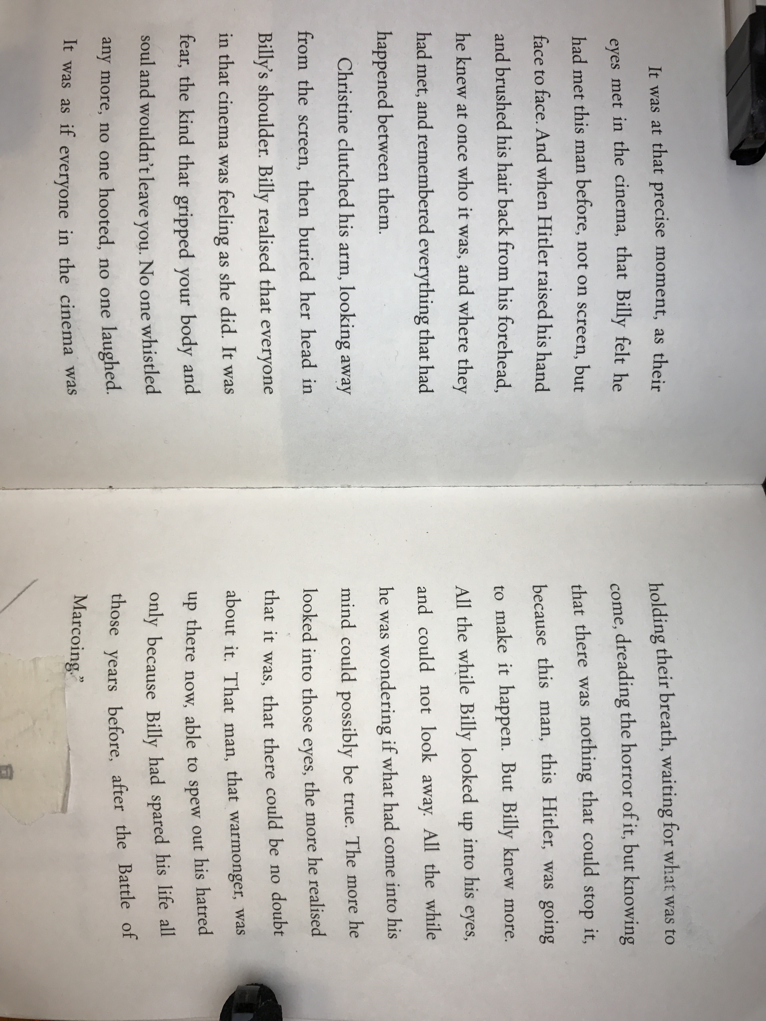
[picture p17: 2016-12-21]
photo/ocr/final.JPG

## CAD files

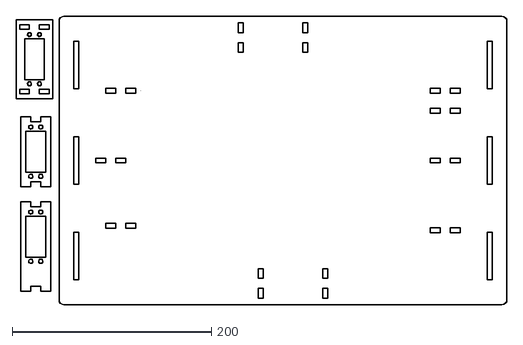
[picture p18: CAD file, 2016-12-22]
hardware/laser-cuts/Mainbaseprint.dxf
493.2 x 290.0

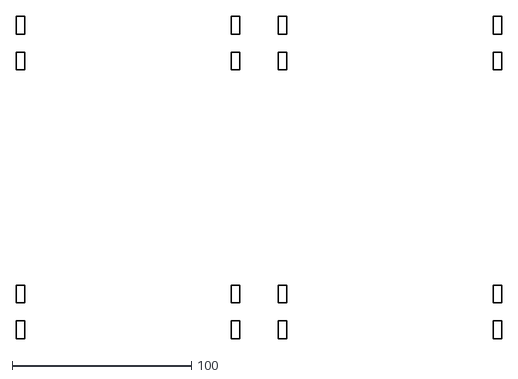
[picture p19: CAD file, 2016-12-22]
hardware/laser-cuts/Mainbase_xtracut.dxf
270.8 x 180.0

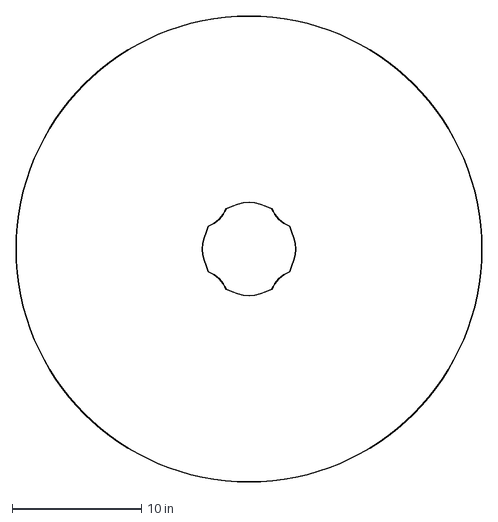
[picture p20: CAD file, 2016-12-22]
hardware/laser-cuts/wheel_slot2.dxf
36.0 x 36.0 in

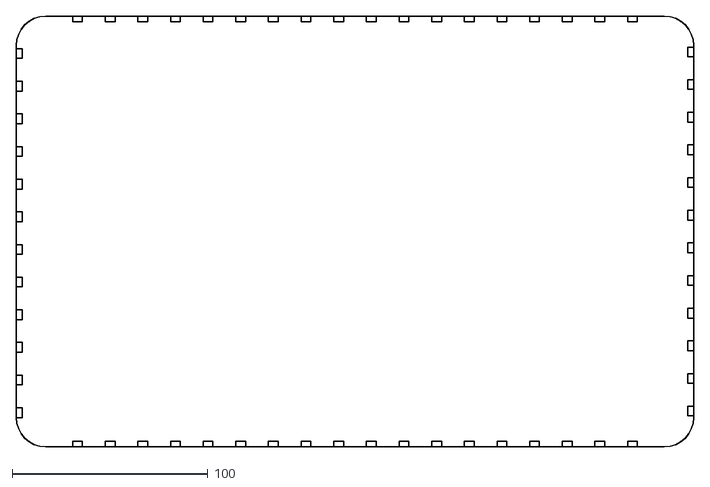
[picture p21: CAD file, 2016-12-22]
hardware/laser-cuts/lightplate.dxf
346.0 x 220.0

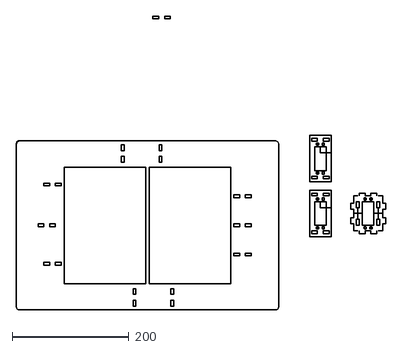
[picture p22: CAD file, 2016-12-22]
hardware/laser-cuts/bookbase2.dxf
633.5 x 504.1

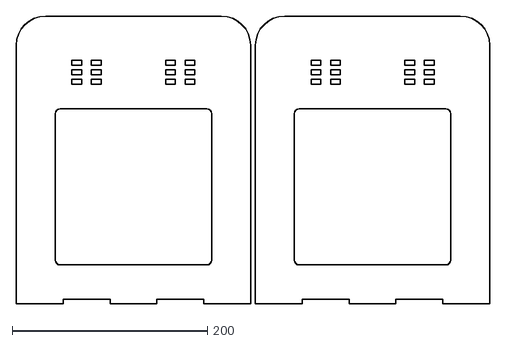
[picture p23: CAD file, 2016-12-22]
hardware/laser-cuts/Supports.dxf
485.0 x 295.0

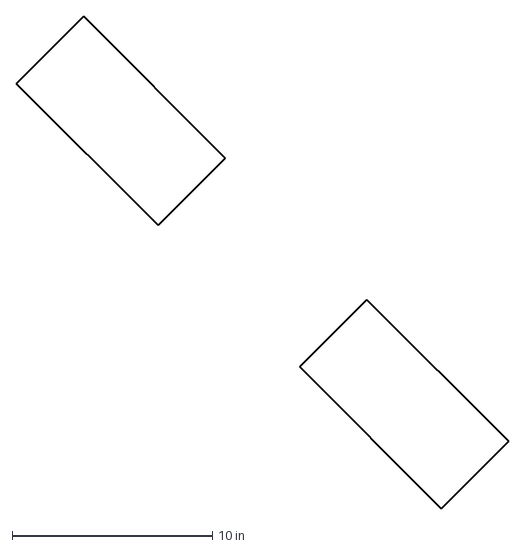
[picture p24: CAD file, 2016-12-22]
hardware/laser-cuts/45degree.dxf
24.6 x 24.6 in

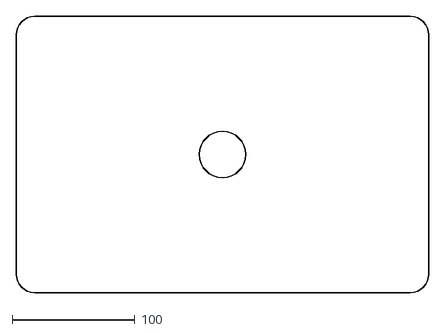
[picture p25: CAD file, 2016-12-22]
hardware/laser-cuts/lightplate_cover.dxf
336.0 x 225.0

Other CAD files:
hardware/laser-cuts/Mainbase.dwg
hardware/laser-cuts/wheel_bracket2.dxf
hardware/laser-cuts/rail_support2.dxf
hardware/laser-cuts/more_brackets.dxf
hardware/laser-cuts/turning_supports.dxf
hardware/laser-cuts/turner_arm.dxf
hardware/laser-cuts/light_supports.dxf
hardware/laser-cuts/pi_mount2.dxf
hardware/laser-cuts/wheel_servo.dxf
hardware/laser-cuts/wheen_bracket.dxf
hardware/laser-cuts/3mm_base_supports.dwg
hardware/laser-cuts/3mm_base_supports.dxf
hardware/laser-cuts/Mainbase_xtracut.dwg
hardware/laser-cuts/Mainbaseprint.dwg
hardware/laser-cuts/ServoBracket.dwg
hardware/laser-cuts/ServoBracket.dxf
hardware/laser-cuts/Supports.dwg
hardware/laser-cuts/base_for_wheel.dxf
hardware/laser-cuts/bookbase2.dwg
hardware/laser-cuts/bookbaseNEW.dwg
hardware/laser-cuts/bookbaseNEW.dxf
hardware/laser-cuts/laotsastuff.dwg
hardware/laser-cuts/lego_slot.dwg
hardware/laser-cuts/lego_slot.dxf
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

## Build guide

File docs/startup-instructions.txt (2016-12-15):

-------TO RUN MAIN SCRIPT-------
cd hcr-2016 [1] [2] [3]
GET THE SERVER ADDRESS FROM: https://github.com/plus44/hcr-2016/blob/master/README.md
ssh -i hcr-2016.pem ec2-user@ec2-54-194-13-254.eu-west-1.compute.amazonaws.com [1]
source ~/venvs/hcr-2016/bin/activate [2]

GET THE RASPBERRY PI ADDRESS FROM: https://github.com/plus44/RPi-IP/blob/master/ip.txt
ssh pi@<<raspi_address>> (password: pinaoqio) [3]

ON SERVER:
cd hcr-2016 [1]
python src/server/main.py -p 80 [1]

ON PI:
cd hcr-2016 [3]
python src/pi/main.py -H ec2-54-194-13-254.eu-west-1.compute.amazonaws.com -p 80 [3]

ON LAPTOP:
python src/laptop/main.py -H ec2-54-194-13-254.eu-west-1.compute.amazonaws.com -p 80 -ri <<robot_ip>> -rp <<robot_port>> [2]

-------TO SEND TURN PAGE COMMANDS:-------
ON LAPTOP:
python src/laptop/pi_turn_page.py -H ec2-54-194-13-254.eu-west-1.compute.amazonaws.com -p 80 [2/4]

-------TO SET WHEEL DEGREES:--------
ON LAPTOP:
python src/laptop/pi_set_wheel_degrees.py -H ec2-54-194-13-254.eu-west-1.compute.amazonaws.com -p 80 -d <<degrees (max 180)>>

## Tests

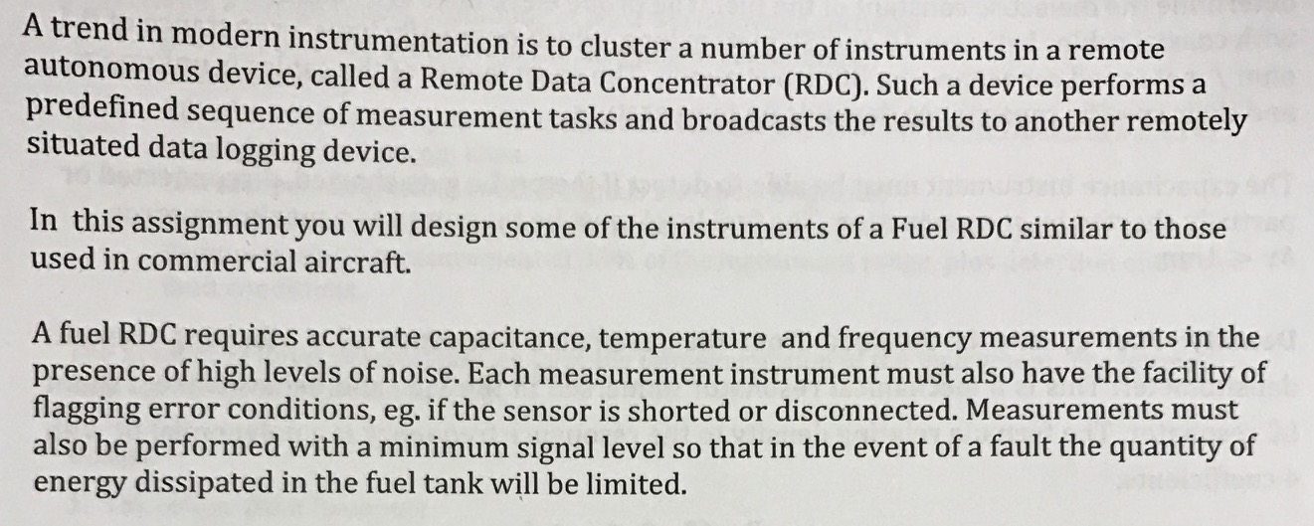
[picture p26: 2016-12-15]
photo/ocr/ocr_test_6.jpeg

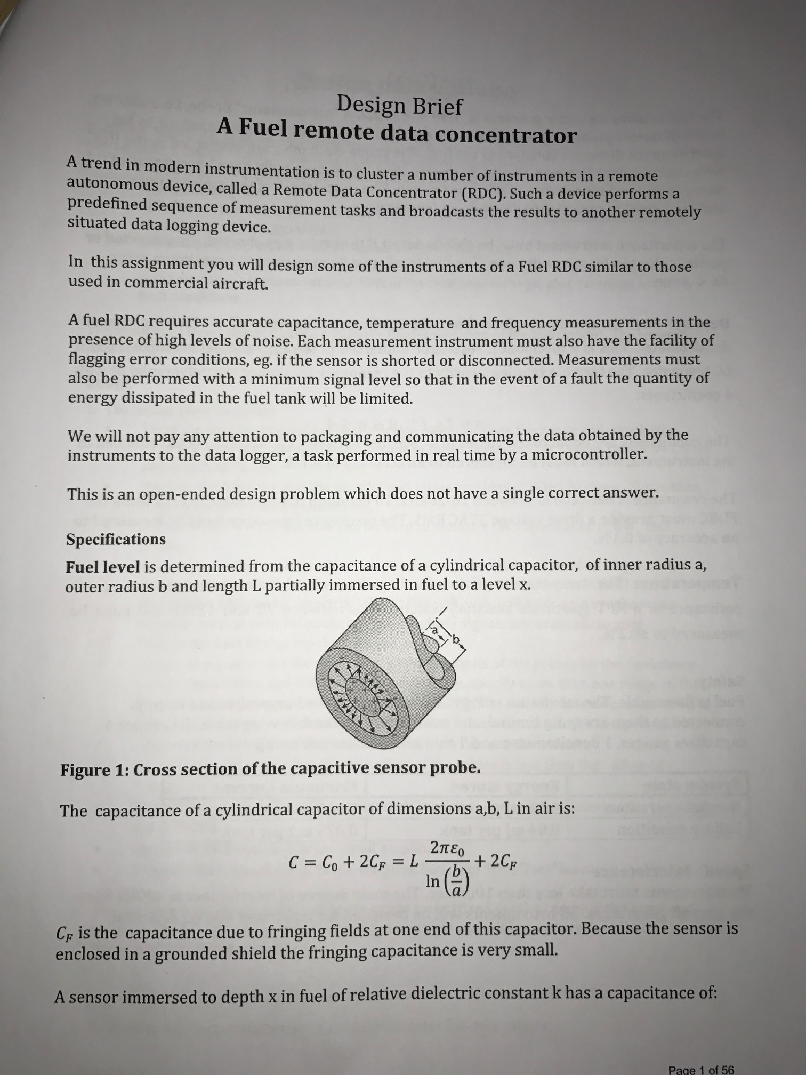
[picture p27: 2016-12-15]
photo/ocr/ocr_test_4.JPG

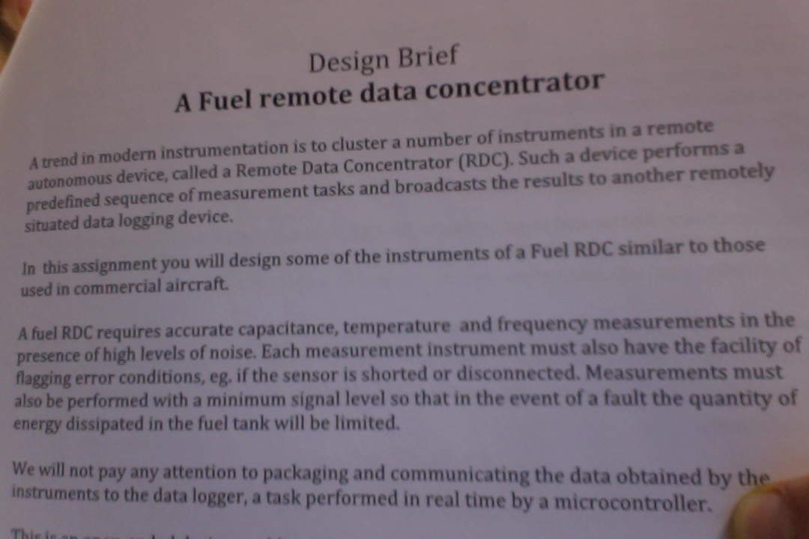
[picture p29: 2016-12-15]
photo/ocr/ocr_test_3.jpg

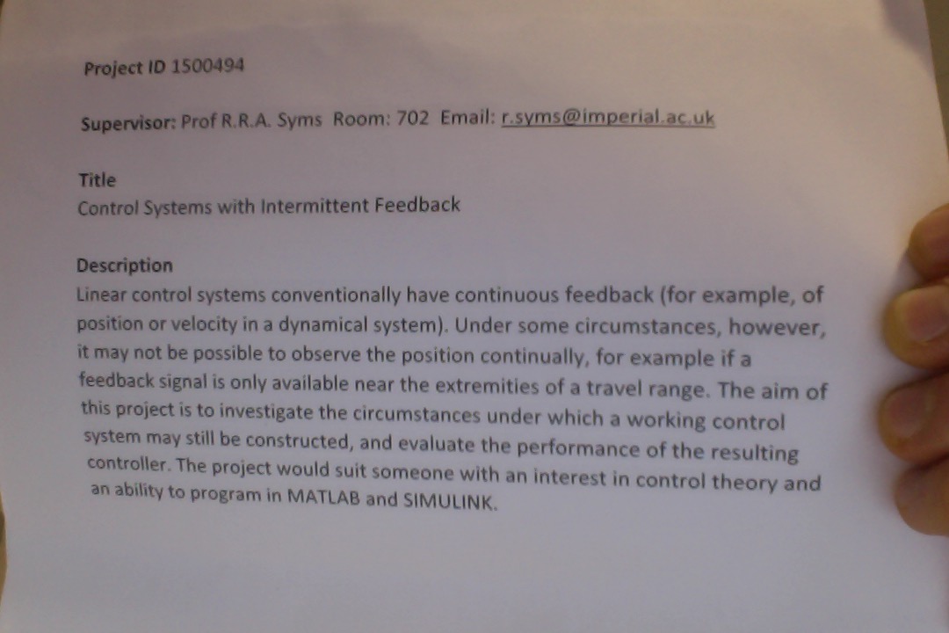
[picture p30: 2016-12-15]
photo/ocr/ocr_test.jpg

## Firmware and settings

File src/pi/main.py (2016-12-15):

#! /usr/bin/python
''' Performs all the HTTP client functions, as well as the page turning 
functions of the Raspberry Pi.
'''

# STANDARD PYTHON IMPORTS
import argparse
import sys
import time

# PYTHON LIBRARIES
import RPi.GPIO as GPIO

# USER LIBRARIES
import enum
from client import RaspberryPiClient
from page_turner import PageTurner

# GLOBAL VARIABLES
LIGHTPLATE_PIN = 20

# CLASSES
class PiStateMachine():
	''' Describes the state machine that handles the server comms and the page 
	turning class.
	'''
	def __init__(self, client=None, page_turner=None):
		''' Initialise the state machine

			'client' is a RaspberryPiClient() instance
			'page_turner' is a PageTurner() instance
		'''
		self._client = client
		self._page_turner = page_turner
		self.state = enum.PiState.QUEUE_LONG_POLL

		self.action = 'doNothing'
		self.is_done_long_polling = False
		self.turned_page = False

		self.lp_pwm = None
		self.lp_pwm_val = 100
		self.init_lightplate_gpio(LIGHTPLATE_PIN, self.lp_pwm_val)

	def __del__(self):
		''' Destructor for the Pi state machine
		'''
		self.lp_pwm.stop()
		self.deinit_all_gpio()

	def init_lightplate_gpio(self, pin, pwm):
		''' Initialises the lightplate GPIO pin.
		'''
		GPIO.setmode(GPIO.BCM)
		GPIO.setup(pin, GPIO.OUT)
		self.lp_pwm = GPIO.PWM(pin, 50)
		self.lp_pwm.start(0)
		self.lp_pwm.ChangeDutyCycle(pwm)

	def deinit_all_gpio(self):
		''' Deinitialises all GPIO initialised in this program
		'''
		GPIO.cleanup()

	def set_client(self, client):
		''' Set up the internal reference to the client.
		'''
		self._client = client

	def set_page_turner(self, page_turner):
		''' Set up the internal reference to the page_turner
		'''
		self._page_turner = page_turner

	def handler_done_long_polling(self, action):
		''' Handler that gets called when the server returns an action from long
		polling.
		'''
		self.action = action
		self.is_done_long_polling = True
		print "Action received from server: %s" % action

	def handler_turned_page(self):
		''' Handler that gets called by the page turner whenever it has finished
		turning a page.
		'''
		self.turned_page = True
		print "Finished turning a page."

	def process_state(self):
		''' Step through the states as needed, queuing tasks in the process.
		'''
		if self.state == enum.PiState.QUEUE_LONG_POLL:
			self._client.queue_long_poll()
			self.state = enum.PiState.WAIT_FOR_ACTION
			return

		elif self.state == enum.PiState.WAIT_FOR_ACTION:
			if self.is_done_long_polling:
				self.is_done_long_polling = False
				self.state = enum.PiState.PROCESS_ACTION
			return

		elif self.state == enum.PiState.PROCESS_ACTION:
			if self.action == 'turnPage':
				self.state = enum.PiState.QUEUE_TURN_PAGE

			elif 'setWheelDegrees' in self.action:
				lst = self.action.split(':', 1)
				try:
					wheel_degrees = int(lst[1])
					self._page_turner.set_wheel_degrees(wheel_degrees)
				except ValueError:
					print "Couldn't convert wheelDegrees %s to int." % lst[1]

				print "Wheel degrees are now: %d" % \
					self._page_turner.get_wheel_degrees()
				# Go back to long polling
				self.state = enum.PiState.QUEUE_LONG_POLL

			elif 'setHolderArmDegrees' in self.action:
				lst = self.action.split(':', 1)
				try:
					holder_arm_degrees = int(lst[1])
					self._page_turner.set_holder_arm_degrees(holder_arm_degrees)
				except ValueError:
					print "Couldn't convert holderArmDegrees %s to int." % \
						lst[1]

				print "Holder arm degrees are now: %d" % \
					self._page_turner.get_holder_arm_degrees()
				# Go back to long polling
				self.state = enum.PiState.QUEUE_LONG_POLL

			elif 'setLightplatePwm' in self.action:
				lst = self.self.action.split(':', 1)
				try:
					self.lp_pwm_val = float(lst[1])
					self.lp_pwm.ChangeDutyCycle(self.lp_pwm_val)
				except ValueError:
					print "Couldn't convert lightplatePwm %s to float." % \
						lst[1]
				# Go back to long polling
				self.state = enum.PiState.QUEUE_LONG_POLL
					
			else:
				print "Invalid action received: %s" % self.action
				# Go back to long polling
				self.state = enum.PiState.QUEUE_LONG_POLL
			return

		elif self.state == enum.PiState.QUEUE_TURN_PAGE:
			self._page_turner.queue_turn_page()
			self.state = enum.PiState.WAIT_FOR_PAGE_TURN
			return

		elif self.state == enum.PiState.WAIT_FOR_PAGE_TURN:
			print "Got to state WAIT_FOR_PAGE_TURN"
			if self.turned_page:
				self.turned_page = False
				print "Posting success server: %s" % self._client.post_success()
				self.state = enum.PiState.QUEUE_LONG_POLL
			return

		else:
			print "Entered invalid state: %s" % self.state
			return


# FUNCTIONS
def main(host, port=80):
	''' Performs the operations of the Raspberry Pi client, connecting to a 
	server on host:port.
	'''
	state_machine = PiStateMachine()

	client = RaspberryPiClient(host, port=port, state_machine=state_machine)
	page_turner = PageTurner(state_machine=state_machine)

	# Set up the recursive references
	state_machine.set_client(client)
	state_machine.set_page_turner(page_turner)

	while True:
		state_machine.process_state()

	# action = client.long_poll()
	# print "Action: %s received from the server." % action

	# if action == "turnPage":
	# 	### Turn page ###

	# 	# Simulate page turn with a delay
	# 	start_time = time.time()
	# 	while (time.time() - start_time < 5.0):
	# 		pass

	# 	print "Page turned: %s" % client.post_success()

def parse_host_and_port(args=None):
	''' Returns a tuple of the parsed address and port arguments from the 
	command line
	'''
	parser = argparse.ArgumentParser(description= \
		"Connects to the server and waits for page turning instructions")
	parser.add_argument('-H', '--host',
						help="Host IP/name",
						required='True',
						default='localhost')
	parser.add_argument('-p', '--port',
						type=int,
						help="Port of the server",
						default=80)

	results = parser.parse_args(args)
	return (results.host, int(results.port))

# CODE
if __name__ == '__main__':
	host, port = parse_host_and_port(sys.argv[1:])
	main(host, port)
else:
	print "Run main.py from __main__."

# END OF FILE

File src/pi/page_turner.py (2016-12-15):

#! /usr/bin/python
''' Performs the hardware level functions of the page-turning mechanism
'''

# STANDARD PYTHON IMPORTS
import subprocess

# PYTHON LIBRARIES
import RPi.GPIO as GPIO

# USER LIBRARIES
from step_servo import ServoStepThread

# GLOBAL VARIABLES
DEFAULT_SETTLING_TIME = 1.0 # second
DEFAULT_WHEEL_DEGREES = 39 # degrees
DEFAULT_HOLDER_ARM_DEGREES = 100 # degrees

# CLASSES
class PageTurner():
	''' Implements the pre-defined page turner actions
	'''
	def __init__(self, state_machine=None):
		''' Initialises the page turner. 

			'state_machine' should contain a reference to a PiStateMachine() 
				object.
		'''
		self._state_machine = state_machine
		self.is_init = False
		self.wheel_degrees = DEFAULT_WHEEL_DEGREES
		self.holder_arm_degrees = DEFAULT_HOLDER_ARM_DEGREES
		# Not needed for bash version
		# self.init_all_servo_gpio()
		self.init_servo_positions()

	def __del__(self):
		''' Destructor for the page turner. Deinit all servo GPIOs
		'''
		# Not needed for bash version
		# self.deinit_all_servo_gpio()
		pass

	def _run_servos(self, pin_lookup):
		''' Runs every servo in the pin lookup table using the src/pi/step_servo.py
		bash script.
		'''
		pin_str = ""
		deg_str = ""
		tim_str = ""

		for pin, tup in pin_lookup.iteritems():
			if pin_str != "":
				pin_str = "%s,%d" % (pin_str, pin)
			else:
				pin_str = "%d" % pin

			if deg_str != "":
				deg_str = "%s,%d" % (deg_str, tup[0])
			else:
				deg_str = "%d" % tup[0]

			if tim_str != "":
				tim_str = "%s,%d" % (tim_str, tup[1])
			else:
				tim_str = "%d" % tup[1]
			
		call_str = 'src/pi/step_servo.py -p "%s" -d "%s" -t "%s"' % \
			(pin_str, deg_str, tim_str)
		print call_str
		subprocess.call(call_str, shell=True)

	def _run_servos_non_bash(self, pin_lookup):
		''' Runs every servo in the pin_lookup table that looks like:
			{ pin : (degrees, settling_time) }
		'''
		threads = []
		for pin, tup in pin_lookup.iteritems():
			threads.append(ServoStepThread(pin, tup[0], tup[1]))

		# Run the servos
		for t in threads:
			t.start()

		# Wait for all servos to settle
		for t in threads:
			t.join()

	def init_all_servo_gpio(self):
		''' Initialises the GPIO module and the individual servo pins
		'''
		self._init_servo_gpio(9)
		self._init_servo_gpio(11)
		self._init_servo_gpio(10)
		self._init_servo_gpio(14)
		self._init_servo_gpio(7)
		self._init_servo_gpio(8)
		self._init_servo_gpio(15)
		print "Successfully init all servo GPIO"

	def _init_servo_gpio(self,pin):
		''' Initialises a single servo GPIO pin.
		'''
		GPIO.setmode(GPIO.BCM)
		GPIO.setup(pin, GPIO.OUT)

	def deinit_all_servo_gpio(self):
		''' Deinitialises all GPIOs
		'''
		GPIO.cleanup()
		print "Successfully deinit all servo GPIO"

	def set_wheel_degrees(self, wheel_degrees):
		''' Sets the wheel degrees value, usually passed from the server through
		the state machine
		'''
		self.wheel_degrees = wheel_degrees

	def get_wheel_degrees(self):
		''' Returns the value of wheel degrees currently in use.
		'''
		return self.wheel_degrees

	def set_holder_arm_degrees(self, holder_arm_degrees):
		''' Sets the holder arm degrees values.
		'''
		self.holder_arm_degrees = holder_arm_degrees

	def get_holder_arm_degrees(self):
		''' Returns the holder arm degrees currently in use
		''' 
		return self.holder_arm_degrees

	def init_servo_positions(self):
		''' Takes the servos to their defined starting positions. 
		'''
		pin_lookup = {9  : (90,  DEFAULT_SETTLING_TIME), \
					  11 : (120, DEFAULT_SETTLING_TIME), \
					  10 : (0,   DEFAULT_SETTLING_TIME), \
					  14 : (180, DEFAULT_SETTLING_TIME), \
					  7  : (100, DEFAULT_SETTLING_TIME), \
					  8  : (75,  DEFAULT_SETTLING_TIME), \
					  15 : (90,  DEFAULT_SETTLING_TIME)}

		self._run_servos(pin_lookup)
		self.is_init = True

	def queue_turn_page(self):
		''' Queues a page turn on a background thread. When the page turning is
		complete, the state_machine's handler_turned_page is called.

		TODO: Background thread
		'''

		# Signal to the state machine that we have finished turning the page
		self.turn_page()
		self._state_machine.handler_turned_page()

	def turn_page(self):
		''' Turns a page using the experimentally adjusted degree values. Calls
		the state_machine's handler_turned_page() function once done.
		'''
		if not self.is_init:
			self.init_servo_positions()
		self.is_init = False

		pin_lookup = {11 : (self.wheel_degrees, DEFAULT_SETTLING_TIME)}
		self._run_servos(pin_lookup)
		pin_lookup.clear()

		pin_lookup = {9  : (0,   DEFAULT_SETTLING_TIME), \
					  15 : (75,  DEFAULT_SETTLING_TIME)}
		self._run_servos(pin_lookup)
		pin_lookup.clear()

		pin_lookup = {15 : (100, DEFAULT_SETTLING_TIME)}
		self._run_servos(pin_lookup)
		pin_lookup.clear()

		pin_lookup = {11 : (120, DEFAULT_SETTLING_TIME), \
					  10 : (130, DEFAULT_SETTLING_TIME), \
					  14 : (0,   DEFAULT_SETTLING_TIME), \
					  7  : (0,   DEFAULT_SETTLING_TIME), \
					  8  : (160, DEFAULT_SETTLING_TIME)}
		self._run_servos(pin_lookup)
		pin_lookup.clear()

		pin_lookup = {7  : (100, DEFAULT_SETTLING_TIME), \
					  8  : (75,  DEFAULT_SETTLING_TIME), \
					  15 : (90,  DEFAULT_SETTLING_TIME)}
		self._run_servos(pin_lookup)
		pin_lookup.clear()

		pin_lookup = {14 : (180, DEFAULT_SETTLING_TIME), \
					  10 : (0,   DEFAULT_SETTLING_TIME)}
		self._run_servos(pin_lookup)
		pin_lookup.clear()


# FUNCTIONS

# CODE
if __name__ == '__main__':
	print "Do not run page_turner.py from __main__."

# END OF FILE

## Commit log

2016-11-09 Added scripts to test: camera and servos on Raspberry Pi, the importing of the Naoqi library
2016-12-02 Added a bit more 'fake' code to Raspberry Pi client.
2016-12-08 Added state machine ffor asynchronous event handling, added OCR capability directly through the tesseract python bindings.
    [client.py, enum.py, main.py]
2016-12-08 Servo stepping program added.
2016-12-09 Multithreading and time delay adjustment (for continuous rotation servos) in src/pi/step_servo.py
2016-12-13 Added Raspberry Pi state machine.
2016-12-13 Added Python scripts in src/laptop to set holder arm and wheel degrees.
2016-12-13 Added turnPage script from laptop to Raspberry Pi
2016-12-13 Renamed wheel and holder arm degree scripts
2016-12-13 Updated a first_start json variable on the laptop side
    [feat.params]
2016-12-13 Fixed a small bug in state_mgr
    [client.py, main.py]
2016-12-13 Hopefully the bug is finally fixed. enum.Device.get_name() should have been enum.Device.get_name[]
2016-12-13 Trying to fix a segfault on the pi
    [main.py, page_turner.py, step_servo.py]
2016-12-14 GPIOs are now initialised in bulk on the Raspberry Pi
2016-12-14 Trying new approach of calling src/pi/step_servo.py from python using shell as opposed to rewriting the threading function in the page_turner class.
2016-12-14 removed mutex on long_poll. very dirty fix, needs rework
    [main.py]
2016-12-14 Lightplate GPIO raspberry pi
2016-12-22 Added laser cutting files for the page turner
    [3mm_base_supports.dwg, 3mm_base_supports.dxf, 45degree.dxf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]
